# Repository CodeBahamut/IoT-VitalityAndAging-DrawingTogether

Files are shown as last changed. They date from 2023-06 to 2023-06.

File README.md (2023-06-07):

# VitalityAndAging - Drawing Together

Studies have shown that it is important for elderly people to keep their creative brain activated. But for some elderly people it is harder to participate in creative activities. And that is why we are designing the Drawbot.

The Drawbot is a robot that can draw together with people. It reacts on what someone has drawn and uses unique movement to make wonderful art. This way elderly people will be able to use their creative brain and improve their cognitive skills without them spending hours having to physically draw.

Current Project Goals For this project we are going to do a lot of research on the technical options and availabilities of the Jetbot. After the research we want to have a Drawbot with the following end goals:

## Markdown Pages Site
To see a more clear site which is more clear and where we put a lot of effort into organizing the information click on this [Pages Link](https://iot.dev.hihva.nl/2022-2023-sep-jan/group-project/vitalityandaging-drawing-together/). For those who just want to browse through the repository look below. 

## Jetbot
Our Drawbot is based on the [Jetbot](https://jetbot.org/master/), we used the body of the Jetbot and modified to our needs by including a penholder that can lift and lower the pen using a servo. We also added an extension to the camera holder to accommodate the changes. We also added a base plate at the bottom to hold the Wemos D1 Mini which is controlling the servo and of course the servo itself. 

## Guide

To find information documentation related to the setup of certain parts and to follow the things we did go to [documentation](./docs/documentation/).

For information on the decisions we made and why we made them and thus the research we did to come to our conclusions go to [research](./docs/research/).

For the product manual go to [product manual](./docs/product_manual.md).
As for the bill of materials you can follow this [link](./docs/bill_of_materials.md).

## Build/Assembly guide

To find out how to build the Drawbot go to the [product manual](./docs/product_manual.md). There you will instructed on the adjustments you need to make to the [Jetbot](https://jetbot.org/master/). Of course you first need the [Jetbot](https://jetbot.org/master/) to be able to follow this guide.

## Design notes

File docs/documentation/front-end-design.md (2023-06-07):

# Front-end design
For the front-end design, we created a wireframe in figma.

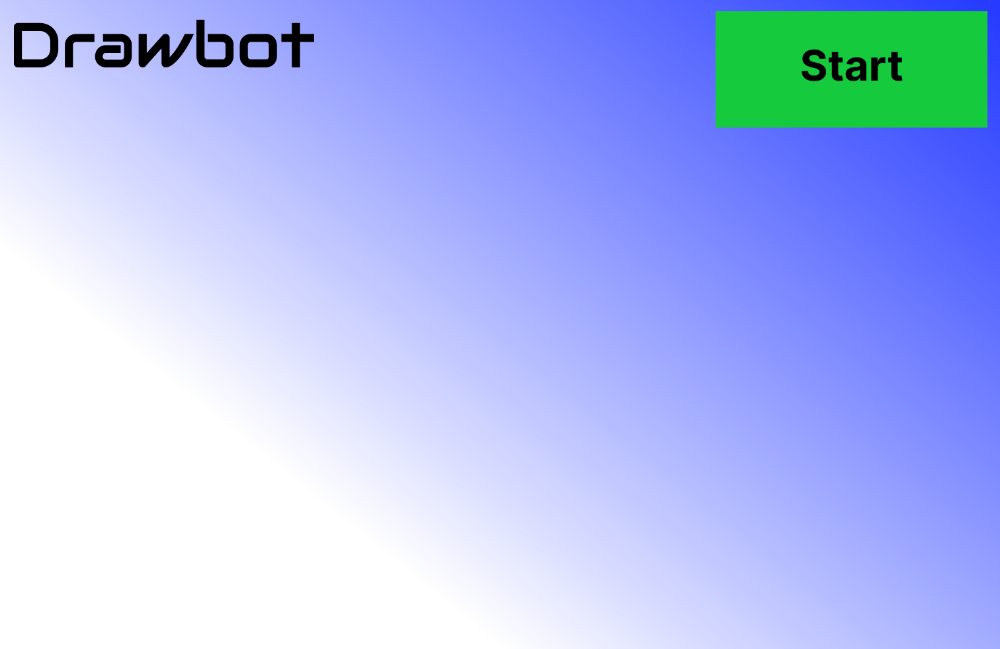
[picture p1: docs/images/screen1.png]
Screen 1

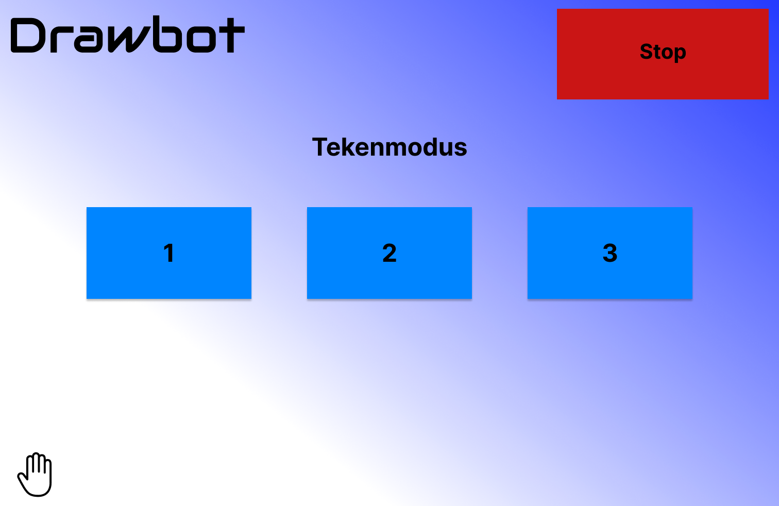
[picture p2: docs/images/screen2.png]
Screen 2

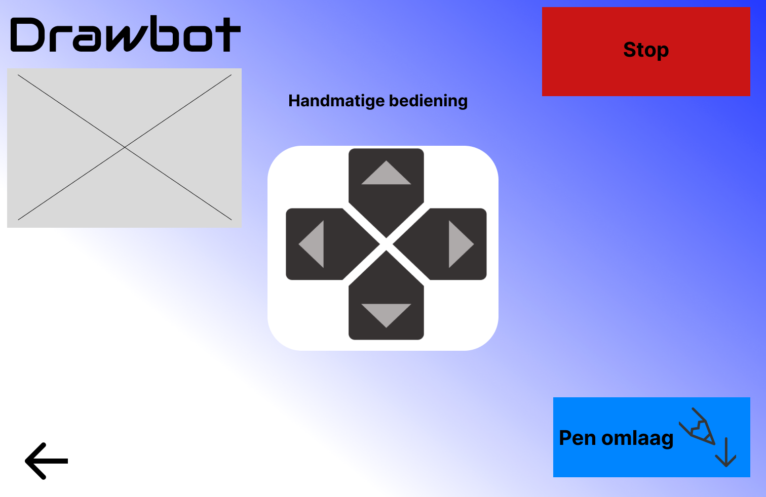
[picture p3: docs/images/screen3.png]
Screen 3


These are rough sketches of what the pages will look like.

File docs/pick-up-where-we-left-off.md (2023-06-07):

# Pick up where we left off

For the next team we advise to go through all the research and documentation we have made. Learn from our mistakes and
improve the DrawBot.

## Project code

[Here](https://gitlab.fdmci.hva.nl/IoT/2022-2023-sep-jan/group-project/vitalityandaging-drawing-together/-/tree/main/embedded-device/drawbot-server-latest-version/drawbot-s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)
you can find the code.

## Our issues

- The power, we noticed that when you're trying to draw and detect shapes at the same time the Drawbot has power issues.
  For more info on the power issues please look into [Power issues](documentation/power_issue.md)
- When we first got the Jetbot it was really hard to connect to it. We have made this way easier, have a look
  into [Jetbot configuration](documentation/jetbot_configuration.md) to set it up.

## Our advice

- We noticed that it is really hard for the Drawbot to make accurate drawings. The motors are not precise enough and
  there is too much fluctuation in the results. Our advice for this would be to use stepper motors. With stepper motors
  you can tell the Drawbot the exact amount of steps it should make. Which should result in more accurate drawings.

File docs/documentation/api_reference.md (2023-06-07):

### API reference

In this table below are all the API calls that can be made to the Drawbot server and some info about them.
Once connected to the hotspot, the Drawbot's server can be reached on jetbot.local:5000

| Endpoint | HTTP METHOD | Description | Response | 
|:---|:---|:---|:---:|
| / | GET | This will return the index page |  HTTP/1.1 200 OK<br>rendered html template (index.html page)  |
| /video | GET | This will push dynamically updated content to the web browser, which is used for streaming the camera's frames | HTTP/1.1 200 OK<br> multipart/x-mixed-replace; boundary=frame |
| /start | POST | This will kick off the Drawbot, by starting a separate thread that will handle the controllers | HTTP/1.1 200 OK<br>{"isDrawBotOn ": "True"} |
| /stop | POST | This will dispose the running thread that is responsible for handling the controllers | HTTP/1.1 200 OK<br>{"isDrawBotOn ": "False"} |
| /start-shape-detection | POST | This will start the shape detection mode, by starting a separate thread that is used to run the shape recognition  | HTTP/1.1 200 OK<br>{"shouldDetectShape ": "True"} |
| /stop-shape-detection | POST | This will stop the shape detection mode, by disposing the thread that is used to run the shape recognition | HTTP/1.1 200 OK<br>{"shouldDetectShape ": "False"} |
| /command/enqueue<br/>/command-type | POST | This will either enqueue or directly fire a certain command, (command-type can be: left, right, forward, backward) | HTTP/1.1 201 OK<br>{"isEnqueued ": "True/False"} |
| /draw-bot-state | GET | This will return the status of the Drawbot | HTTP/1.1 200 OK<br>{"isDrawBotOn ": "True/False"} |
| /pen-up | POST | This will send a signal to the Wemose, to set the pen up | HTTP/1.1 200 OK<br>{"isPenUp ": False} |
| /pen-down | POST | This will send a signal to the Wemose, to set the pen down | HTTP/1.1 200 OK<br>{"isPenUp ": True} |
| /flower-1 | POST | This will make the Drawbot to draw a flower v1 | HTTP/1.1 200 OK<br>{"drawing-flower-1": True} |
| /flower-2 | POST | This will make the Drawbot to draw a flower v2 | HTTP/1.1 200 OK<br>{"drawing-flower-2": True} |
| /flower-3 | POST | This will make the Drawbot to draw a flower v3 | HTTP/1.1 200 OK<br>{"drawing-flower-3": True} |

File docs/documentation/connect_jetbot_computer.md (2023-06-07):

# How to connect Jetbot to a computer

### Installing OS

If the Jetbot has the OS already installed on the SD card and configured you can skip this part.
If not click on the drop down menu below and follow the steps.

<details>
<summary> How to install OS and flash it onto SD card </summary>
<br> 

### Step 1

Go to the [Jetbot doc site](https://jetbot.org/master/software_setup/sd_card.html) and the Jetbot SD card image. The Jetbot for our project has the Jetson Nano (4GB) so make sure you choose the correct download file. 

### Step 2 

1. Insert an SD card into your desktop machine

2. Using [Etcher](https://www.balena.io/etcher/), select the image you downloaded above and flash it onto the SD card.

3. Remove the SD card from your desktop machine

</details>

### Boot Jetson Nano 

1. Insert the SD card into your Jetson Nano (the micro SD card slot is located 
   under the module)

2. Connect the monitor, keyboard, and mouse to the Nano

3. Power on the Jetson Nano by connecting the micro USB charger to the port

### Connecting to Wifi

Next you'll need to connect to WiFi.

1. Log in using the user ``drawbot`` and password ``Drawbotteam01``.
   If you're doing this off a fresh install the user is ``jetbot`` and password ``jetbot``.

2. Connect to a WiFi network using the following command

    ```bash
    sudo nmcli device wifi connect <SSID> password <PASSWORD>
    ```

Your Jetson Nano should now automatically connect to the WiFi at boot and display it's IP address on the piOLED display.

### Connect to Jetbot using browser

1. Shutdown JetBot using the command line

    ```bash
    sudo shutdown now
    ```

2. Unplug your HDMI monitor, USB keyboard, mouse and power supply from Jetson Nano

3. Power the JetBot from the USB battery pack by plugging in the micro-USB cable

4. Wait a bit for JetBot to boot

5. Check the IP address of your robot on the *piOLED* display screen.  Enter this in place of ``<jetbot_ip_address>`` in the next command

6. Navigate to ``http://<jetbot_ip_address>:8888`` from your desktop's web browser. You can do this from any machine on your local network.  

7. Sign in using the password ``Drawbotteam01`` (if that doesn't work try ``jetbot``).

You will be presented with a view similar to the following. 

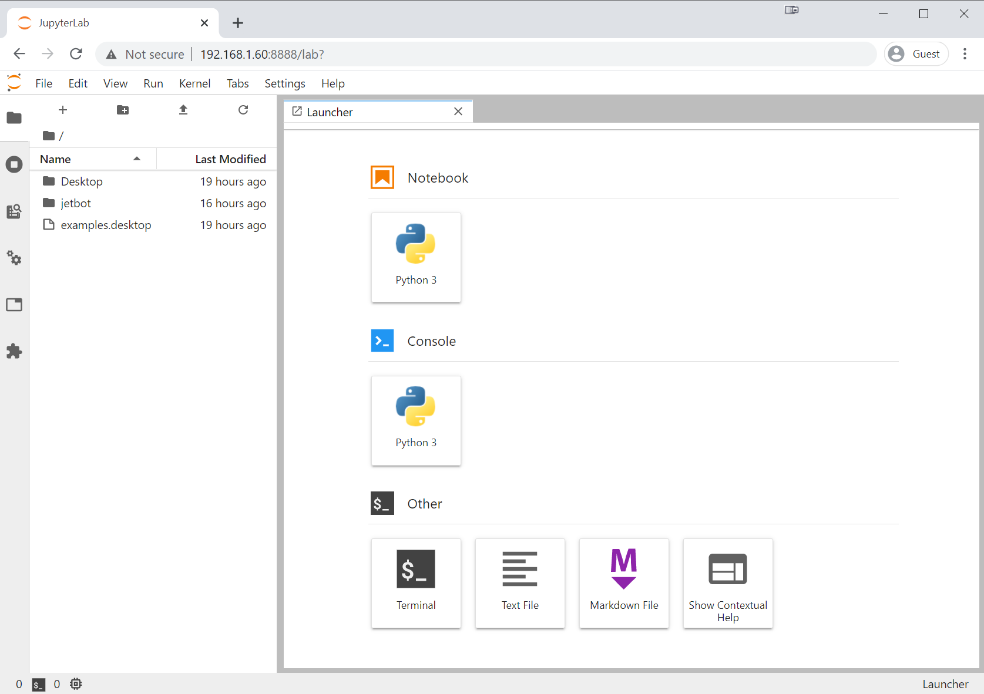
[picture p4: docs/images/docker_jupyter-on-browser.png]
jupyter on browser


From this point on, when you power on the JetBot, it should automatically connect to WiFi and display it's IP address.  So all you need to do is reconnect using your web browser to start programming!

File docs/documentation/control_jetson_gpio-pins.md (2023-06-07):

# Controlling the GPIO pins on the Jetson Nano 

### RPi GPIO

After following the guide below we managed to figure out how to control the GPIO pins on the Jetson nano. The OS comes with the RPi.GPIO library and if not you need to install it.

<iframe width="280" height="160" 
src="https://www.youtube.com/embed/BBKpEgJKF0s" 
title="YouTube video player" frameborder="0" allow="accelerometer;
autoplay; clipboard-write; encrypted-media; gyroscope; picture-in-picture" allowfullscreen></iframe>

Using this video I came up with the code for the next example.

```python
import RPi.GPIO as GPIO
import time   
class PenServo:
    
    def __init__(self, pin):
        self.pin = pin
        # Optional cleanup which resets GPIO states
        GPIO.setmode(GPIO.BOARD)
        GPIO.cleanup(pin)
        # Setup
        GPIO.setup(pin,GPIO.OUT)
        self.is_up = True
        
    def up(self, delay = 0):
        GPIO.output(self.pin,True)
        time.sleep(delay)
        self.is_up = True
        
    def down(self, delay = 0):
        GPIO.output(self.pin,False)
        time.sleep(delay)
        self.is_up = False
```

Here we use the RPi GPIO library to control the pins. Then we set the mode to board mode. Which means that you give it the pin numbers that are visible on the actual board. 
We cleanup the code to make sure its hasn't been configured or used for something else at the same time. We then set it as an output pin. We also add a state variable in the form of is_up to keep track of weather the servo is facing up or down. According to the code that we have on the Wemos if the pin is positive it will go up and if its negative it will go down. 

Below is an example using Jetson GPIO but we found this to be less intuitive than RPi.GPIO so we didn't use but it might prove handy for someone else. 

[NVIDIA/jetson-gpio](https://github.com/NVIDIA/jetson-gpio)

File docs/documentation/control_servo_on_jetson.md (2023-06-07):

# Servo on the Jetson Nano

In this documentation we will explain how we went about trying to get a servo working on the Jetson Nano, where we looked, 
what we found, what we ended up doing and the conclusion we came to. 

## Using the Wemos D1 to Control the servo according to a signal from the Jetson Nano. 

We use a Wemos D1 mini to control the servo while it receives a signal from the Jetson Nano. In our use case we only need the servo to switch between 2 states. So we came to the conclusion that 1 pin signal is enough since if we switch the signal from positive to negative thats 2 states and that fulfills our requirement. We used the GPIO pin to send a signal to the Wemos. For an explination on how we used the GPIO pins go to [Jetson GPIO pins.](documentation/control_jetson_gpio-pins.md) 

On the Wemos we used the following code 

```cpp
#define COMMAND_PIN D2
#define SERVO_PIN D4
#include <Servo.h>
Servo servo;

// the setup routine runs once when you press reset:
void setup() {
  Serial.begin(115200);
  pinMode(COMMAND_PIN, INPUT_PULLUP);
  servo.attach(SERVO_PIN);
}

// the loop routine runs over and over again forever:
void loop() {
  // read the input pin:
  int inputState = digitalRead(COMMAND_PIN);
  // print out the state of the servo:
  Serial.println(inputState);
  if(inputState == HIGH){
    servo.write(180);
    delay(1000);
  } else if(inputState == LOW){
    servo.write(0);
    delay(1000);
    } 
}
```

As you can see we assign pin D2 on the servo to the pin from the Jetson Nano so essentially its the input pin. While we assign pin D4 to the servo to control it. 
We then setup the input pin as a pullup so that we can get a consistent reading. We then print out the state for debugging purposes and we make a if statement for it to check weather the pin is on high or low and move the servo accordingly. 

For the Jetson nano side we made a class to control the pin.

```python
import RPi.GPIO as GPIO
import time   
class PenServo:
    
    def __init__(self, pin):
        self.pin = pin
        # Optional cleanup which resets GPIO states
        GPIO.setmode(GPIO.BOARD)
        GPIO.cleanup(pin)
        # Setup
        GPIO.setup(pin,GPIO.OUT)
        self.is_up = True
        
    def up(self, delay = 0):
        GPIO.output(self.pin,True)
        time.sleep(delay)
        self.is_up = True
        
    def down(self, delay = 0):
        GPIO.output(self.pin,False)
        time.sleep(delay)
        self.is_up = False
```

For an explication on how it works you can go again to our documentation on [Jetson GPIO pins.](documentation/control_jetson_gpio-pins.md) 

The wiring diagram is: 

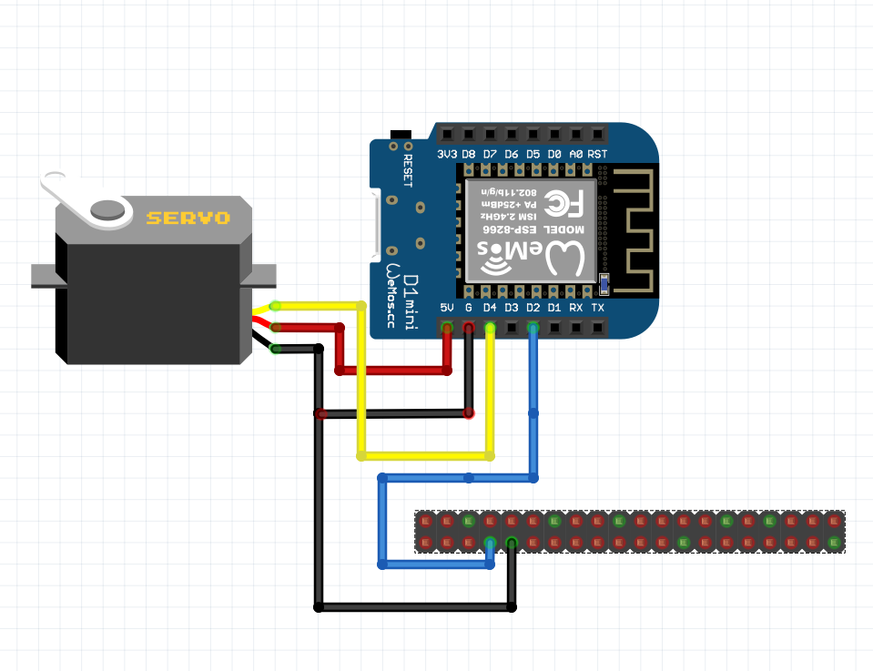
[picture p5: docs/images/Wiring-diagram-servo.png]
Wemos-Jetson-Wiring-Diagram


## Failed Attempt 1: Connecting servo directly to Jetson Nano

Initially we tried to connect the servo directly to the Jetson nano. After some research we found a few ways to do it. 
The first way was to turn on one of the PWM pins on the Jetson nano which do exist but they are disabled by default. 
The second method was to use the PCA9685 PWM module which is a module for adding servos to an embedded device if you 
lack PWMs or if you just want more than you currently have. 

We tried to turn on the PWMs pins by configuring the Jetson expansion headers using with the method on the
[nvidia Jetson nano documentation](https://docs.nvidia.com/jetson/archives/r35.1/DeveloperGuide/text/HR/ConfiguringTheJetsonExpansionHeaders.html). 

This didn't work and every time we tried to run the jetson-io.py file we would get an error. 
We tried to attempt to change the files ourselves without running the file, but we didn't get it working. 
After 2 days of tinkering with it, we came to the conclusion that because of the custom OS of the Jetbot 
we lacked certain directories/dependencies to get it to work, so we moved on to the next method.
gave up and tried the next method. 

Here are some sources we tried using that didn't fix our problem but did provide a lot of guidance:

[Jetson Nano Developer Kit User Guide](https://developer.nvidia.com/embedded/downloads#?search=Jetson%20Nano%20Developer%20Kit%20User%20Guide)

<iframe width="280" height="160" 
src="https://www.youtube.com/embed/eImDQ0PVu2Y" 
title="YouTube video player" frameborder="0" allow="accelerometer;
autoplay; clipboard-write; encrypted-media; gyroscope; picture-in-picture" allowfullscreen></iframe>

## Failed Attempt 2: Connecting the servo to the Jetson Nano using a PCA9686 PWM module

After our first failed attempt we ordered the module and tried running it with the Jetson Nano. 
We ran into 2 major problems with this module. 

The first one was that we got errors caused by the python version we were using. We thought about updating it but because we were using TensorRT and it needed other libraries and dependencies tp be a certain version or release which meant we couldn't just randomly update the python version. 

When we tested the I2C connection to the PCA9686 we got a response and confirmed that the Jetson was able to see it. We downloaded circuit python to use the adafruit-servokit library. But here we got the errors related to the python versions and we couldn't find a feasible solution. We also had problems related to the GPIO rules, to control the permissions we needed to adjust the gpio rules files but that file wasn't there with our version of the OS. So we ended up scraping this idea and decided to use a Wemos D1 mini to control the servo.

Here are some sources we tried using that didn't fix our problem but did provide a lot of guidance:

[Circuit Python Guide](https://learn.adafruit.com/circuitpython-libraries-on-linux-and-the-nvidia-jetson-nano/initial-setup)

[https://github.com/JetsonHacksNano/ServoKit](https://github.com/JetsonHacksNano/ServoKit)

<iframe width="280" height="160" 
src="https://www.youtube.com/embed/RnGUTny1hG8" 
title="YouTube video player" frameborder="0" allow="accelerometer;
autoplay; clipboard-write; encrypted-media; gyroscope; picture-in-picture" allowfullscreen></iframe>

<iframe width="280" height="160" 
src="https://www.youtube.com/embed/28Hj8if8fNY" 
title="YouTube video player" frameborder="0" allow="accelerometer;
autoplay; clipboard-write; encrypted-media; gyroscope; picture-in-picture" allowfullscreen></iframe>

<iframe width="280" height="160" 
src="https://www.youtube.com/embed/8YKAtpPSEOk" 
title="YouTube video player" frameborder="0" allow="accelerometer;
autoplay; clipboard-write; encrypted-media; gyroscope; picture-in-picture" allowfullscreen></iframe>

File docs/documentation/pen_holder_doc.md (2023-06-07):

### Sprint 1

In this documentation file we will explain how we made the pen holder extension for the JetBot. First we downloaded the original JetBot files from their [markdown page](https://jetbot.org/master/bill_of_materials.html) and loaded them into Fusion360 and Tinkercad. Because we did not yet know which software we were going to use we tried both. As Fusion360 is the most elaborate program we thought that would be the best option. The only downside of Fusion360 is that there is a big learning curve to learn the functions required to make the design. The downside of Tinkercad is that you can only create basic shapes. We divided the programs between two of the teammates and the person who was working with Tinkercad soon found out that creating a design with Tinkercad worked perfect. So we continued with that. 

After loading the original files into the program we discussed how we were going to attach a pen to the previously researched best location in between the wheels of the Bot. We soon found out that it was far too difficult to place the pen exactly in the middle because we then had to move the Jetson Nano and the battery. So we concluded that we would move the camera mount further to the front and place the pen behind it in front of the robot. Here is an image with a rough sketch of how we wanted it to turn out.

Rough sketch

What we did in this step is load in 2 camera mounts. With one we chopped off the top and with the other we chopped off the bottom so we could rotate the mount. We knew we wanted no limitations in what kinds of writing material we could use so we made a practice pen (the invisible cilinder you see) 2cm in diameter. From this we knew how far we needed to place the camera mount. 

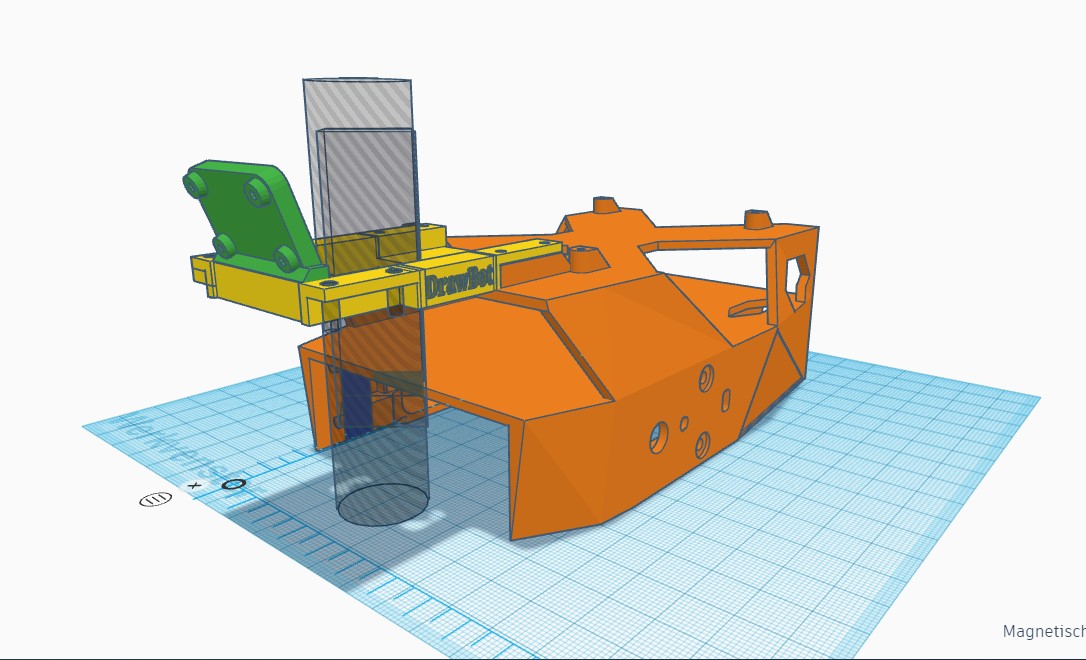
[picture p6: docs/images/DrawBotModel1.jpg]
Extensions complete


In the image above you can see how we attached the extension to the JetBot. We did this by loading in another camera mount and bridging the gap between those two with a box section. For added detail we put the text "DrawBot" on there. After that we filled in the space between those box sections and made a circular hole to fit the marker in. This was a 2cm diameter hole, this because the biggest marker is about that size so there would not be any restrictions. When that hole was created we started thinking of ways to fasten the marker on the design. We quickly came up with a system where two triangular cutouts could keep the marker in place after which a bolt of some sort could be tightened to squeeze against the marker to stop it from sliding out. These triangular cutouts are also useful when you want to install a different size pencil because the smaller the pencil the further it would get to the tip of the triangle.

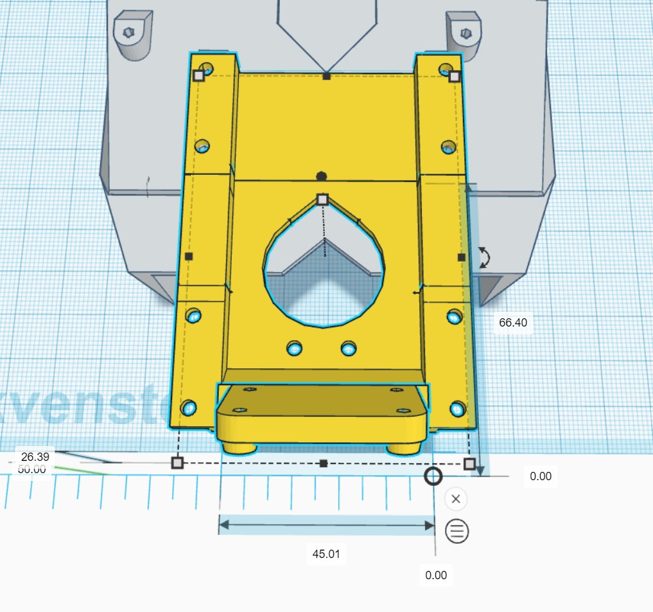
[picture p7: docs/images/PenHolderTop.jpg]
Cutout for the marker


Then we needed to make sure the whole design would not wiggle so the pen could not skip around on the paper. To achieve this we made use of 4 existing holes on the bottom of the JetBot and attached diagonal supports to it. We wanted these to resemble the structure of the JetBot which meant a lot of diagonal angles. This was a bit of a challenge to make in Tinkercad because of the limitation to normal shapes. But with some messing around we managed to get the supports diagonal from the side and from the front. 

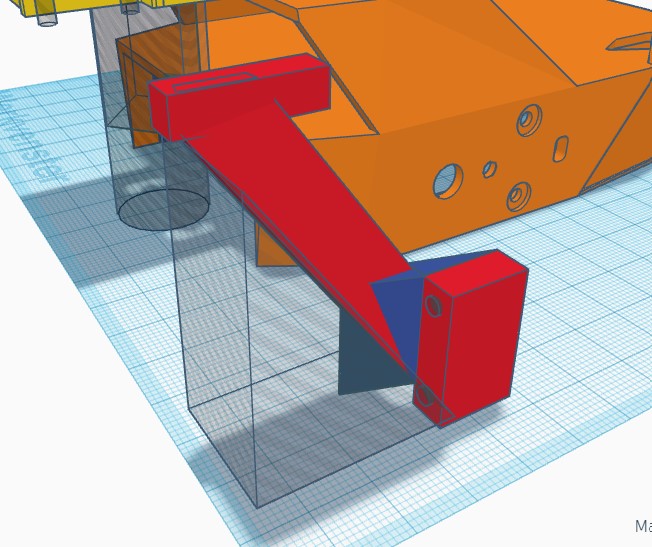
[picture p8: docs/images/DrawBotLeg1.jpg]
Drawbotleg1

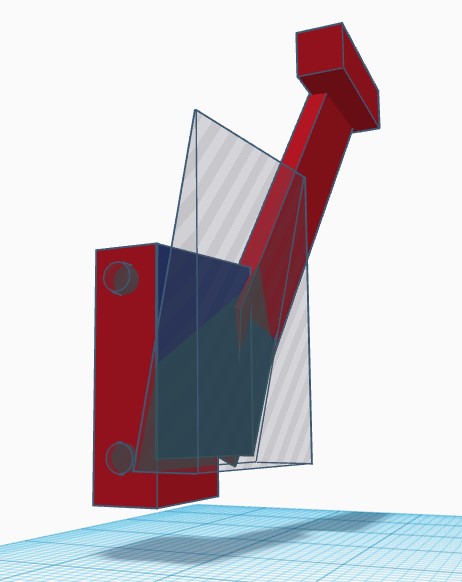
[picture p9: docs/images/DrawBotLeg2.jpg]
Drawbotleg2


In the images above you can see one of the legs that holds the camera mount steady. We made this by rotating a rectangular beam about 45 degrees and then attach it to two triangular shapes (blue bits). Aftre this we cut away the excess material by combining the support with two triangular holes as seen in the image. We copied and rotated one leg to fit on the other side. This in how the supports turned out.

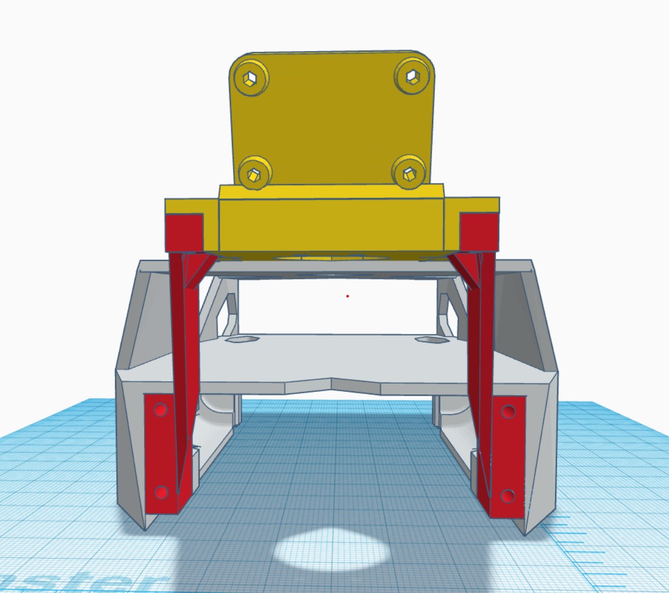
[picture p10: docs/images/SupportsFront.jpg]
SupportsFront

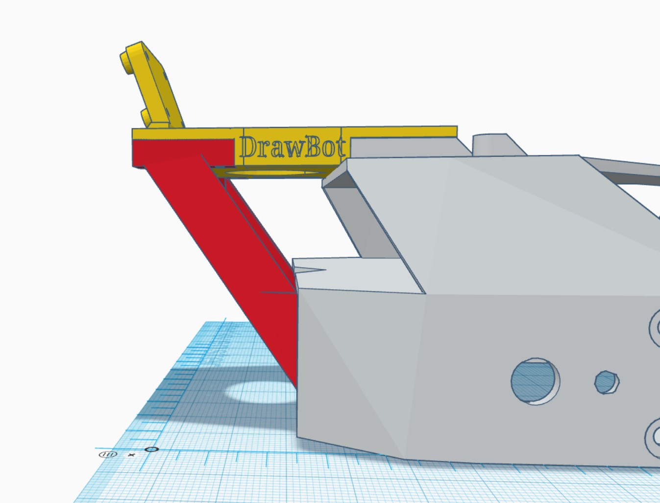
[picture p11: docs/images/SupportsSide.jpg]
SupportsSide


Lastly we needed to figure out a way to attach the bolt which squeezes against the marker. At first we wanted to make a hole just underneath where the camera sits but we came to the conslusion that the bolt would only press the marker against the top triangle and it would wiggle freely on te bottom triangle. So we made a little underhang with a hole big enough for the bolt and attached it using screws. Unfortunatly the first design we made was not big enough to put the bolt through and still be able to twist it with your fingers so we had to make it bigger. 

Failed Wedge

We made the wedge bigger to be more sturdy and so it could fit an M5 bolt. We decided that the M5 bolt should be a hex bolt because of the relatively smaller head. The only dwonside of a hex bolt is that its head is round so you would not be able to grip it to twist is. To resolve this we made a slide-over system that would make the hex bolt easier to twist. These can be seen in the image below.

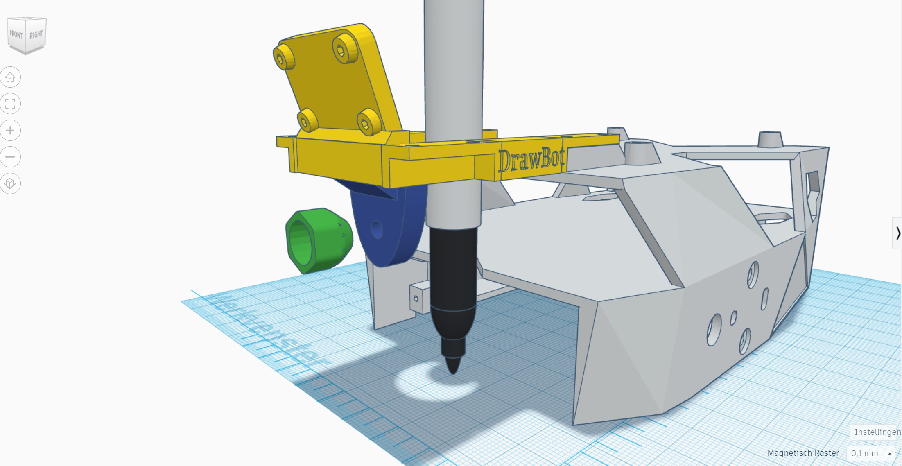
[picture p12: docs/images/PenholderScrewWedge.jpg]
ScrewWedge


All we had to do now was slice the design and print it. This process was no trouble as the program Ultimaker Cura created all the supports. One little mishap we noticed when the print was done was that we had placed the two legs the wrong way around so the program made printing supports on the outside. This turned out pretty ugly so we might change that later. You can click the black play button for a video.

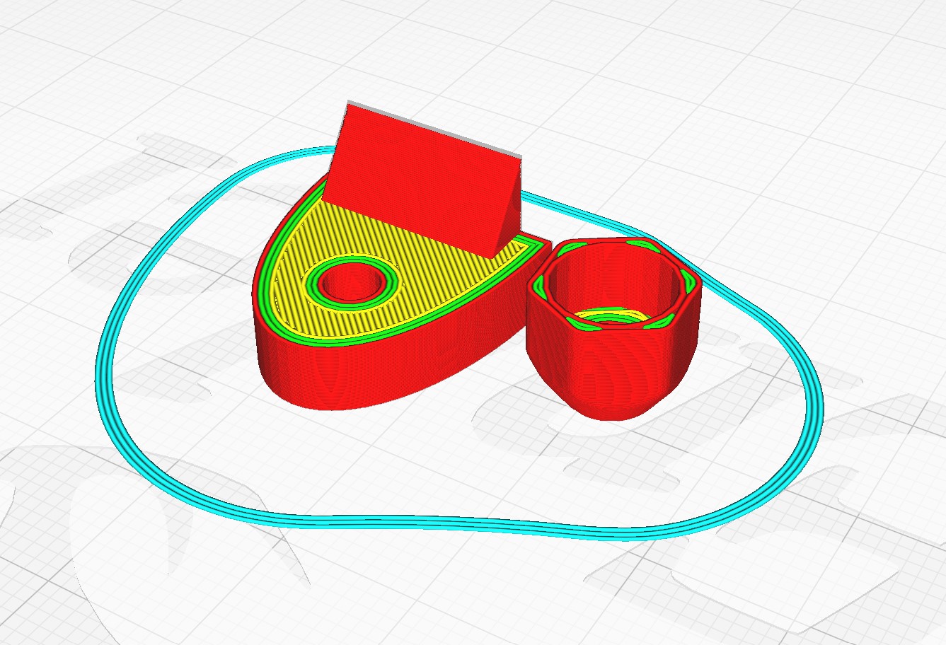
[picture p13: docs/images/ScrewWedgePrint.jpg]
WedgeScrewPrint

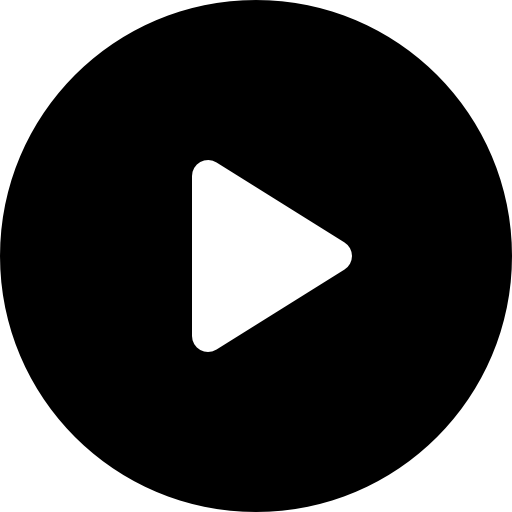
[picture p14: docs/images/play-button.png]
Penholderprint.MP4


<b>And after printing and attaching it looks like this!</b> 

HolderSide
HolderFront
HolderTop

It fit perfectly! There were no gaps and the screws could slide in like they had always been there. There were however some difficulties. The hole where the big screw fits through was not big enough to thread but this was resolved with brute force. The second issue was that the supports that were made for the 3d printer were too firm and were quite hard to remove. So after they were gone it looked like this:

Leg Before

We cleaned this up by wet sanding it and after that it turned out like this:

Leg After

### Sprint 2

For this sprint we want to change a couple of things:

- We need to be able to lift the pen off of the paper. This is going to be done with a servo.

- We need to get 4 M2 X 20 screws for the bottom of the legs, we could not find these anywhere. 

- And lastly we want to adjust the angle of the camera so it points more downward.

We started with adjusting the angle of the camera by loading the existing design in a new tinkercad file. Then we started to look around the design for how we could make the camera point down more. Soon we came up with a system where the camera could rotate so we could change the angle whenever we wanted to. This is what we came up with:

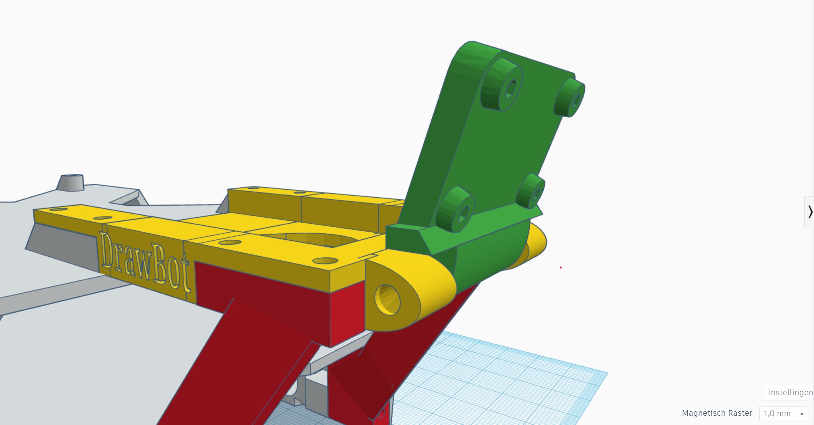
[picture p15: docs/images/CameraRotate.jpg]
Rotateable Camera


The idea is that there would be a bolt and a nut going through the holes. Once this is tightened the yellow part will clamp the green part holding the camera steady. We have not been able to test it as it is not done printing while this is being written. (Update: the model is done printing and it turned out pretty good. The only thing we had to do was make the holes a little bit bigger because the bolt would not slide through easily.)

After this was done we had to find a way to lift the pen off of the paper with a servo. We got inspiration from [this](https://youtu.be/tF2mantrnuI) video where the pen is in a seperate box. The box is on guides and is being pushed up by the servo and pushed down by springs. After some tinkering in Tinkercad it turned out like this: 

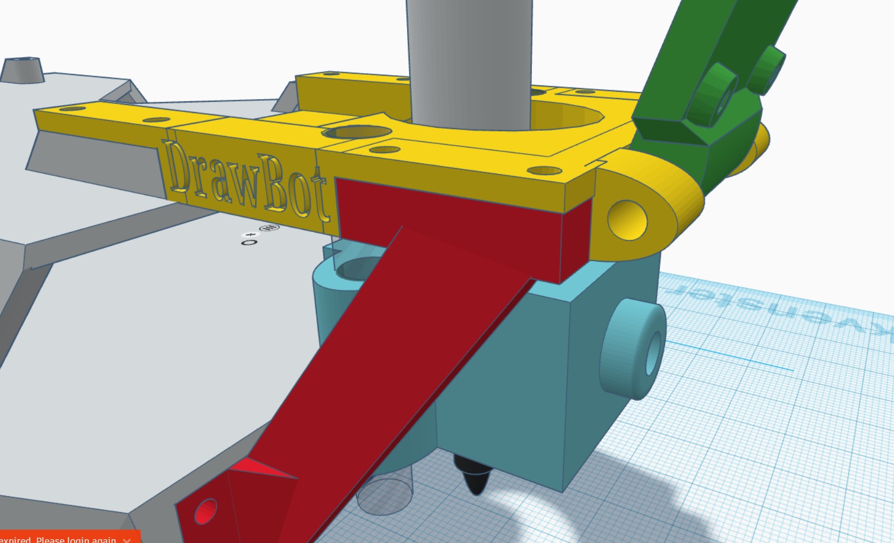
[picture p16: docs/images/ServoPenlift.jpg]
Pen lift side

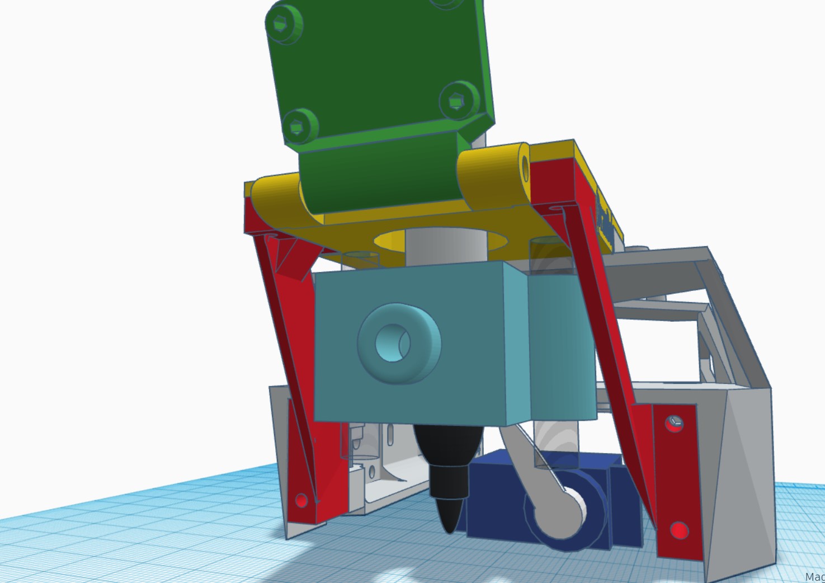
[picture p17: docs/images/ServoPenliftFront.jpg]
Pen lift front


The hole in the front of the light blue part is for an M5 bolt to clamp the pen in place. Just with the old design this part has a triangular hole so there is no limitation in what type of pen it fits. On the side of the blue parts there are two holes that are slightly bigger than an M6 bolt so that it can slide up and down. The bolts attach on the yellow part where we are going to tap the holes. If everything is sized properly the arm of the servo should just about hit the sliding part. 

After making this we had to find a way to attach the servo and the chip to control it. So we took another look at the existing JetBot and discovered 4 existing holes at the bottom. We used those to create a floor where the chip and servo could be attached. After designing it looked like this: 

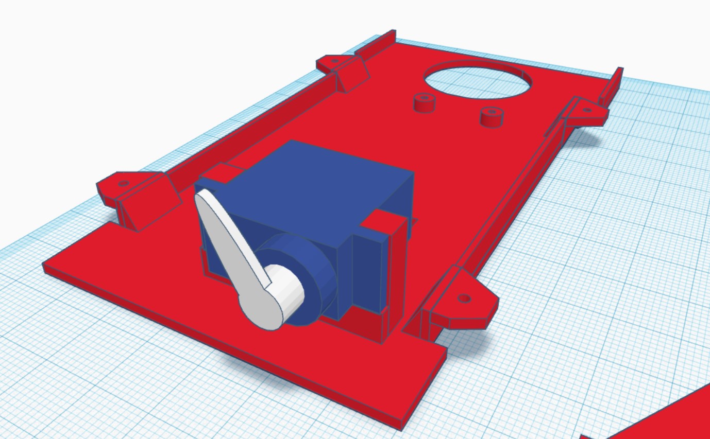
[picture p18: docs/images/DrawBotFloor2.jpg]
Floor


The floor is lower than the bottom of the JetBot because the chip we want to use is quite tall and when that is attached it hits the other chip that controls the motors. The servo uses its own mounting points.

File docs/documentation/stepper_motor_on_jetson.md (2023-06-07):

# Stepper Motors on the Jetson Nano 

## DC Motors vs Stepper Motors

### DC Motors

DC motors are electrical motors that move depending on the polarity of the magnets inside them. The polarity is determined by the the current that is flowing through it and the direction of the current. 

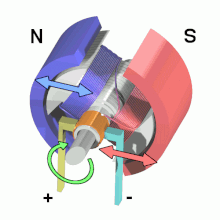
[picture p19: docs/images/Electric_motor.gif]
Electric Motor animation


As you can see in the animation above, the inside is covered in coils that change polarity depending on the direction of the current running through them and the outside are 2 magnets that repel/attract the magnets depending on their polarity. 

The fact that the DC motors can only be set on or off also means that they are hard to stop on a set point and thus hard to use for accurate movements. This fact is of importance to our project since we need accuracy to draw using the Drawbot. 

The video below goes more in depth on how electric motors work if you want to learn more. 

<iframe width="480" height="270" 
src="https://www.youtube.com/embed/CWulQ1ZSE3c" 
title="YouTube video player" frameborder="0" allow="accelerometer;
autoplay; clipboard-write; encrypted-media; gyroscope; picture-in-picture" allowfullscreen></iframe>

### Stepper Motors

Stepper motors work in principle the same as the DC motors. The main difference between the two is that DC motors have the coils mainly on the inside and the change in polarity happens in those coils to spin. While with the stepper motors the object with the set polarity is in the middle and the coils are on the outside ring. 

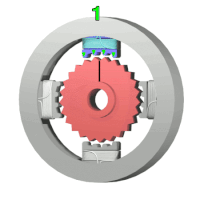
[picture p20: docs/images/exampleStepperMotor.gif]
Stepper Motor


As you can see in the example animation above the disk in the middle which is called the rotor gets spun around by changing the polarity of the motor which is called a stator. 

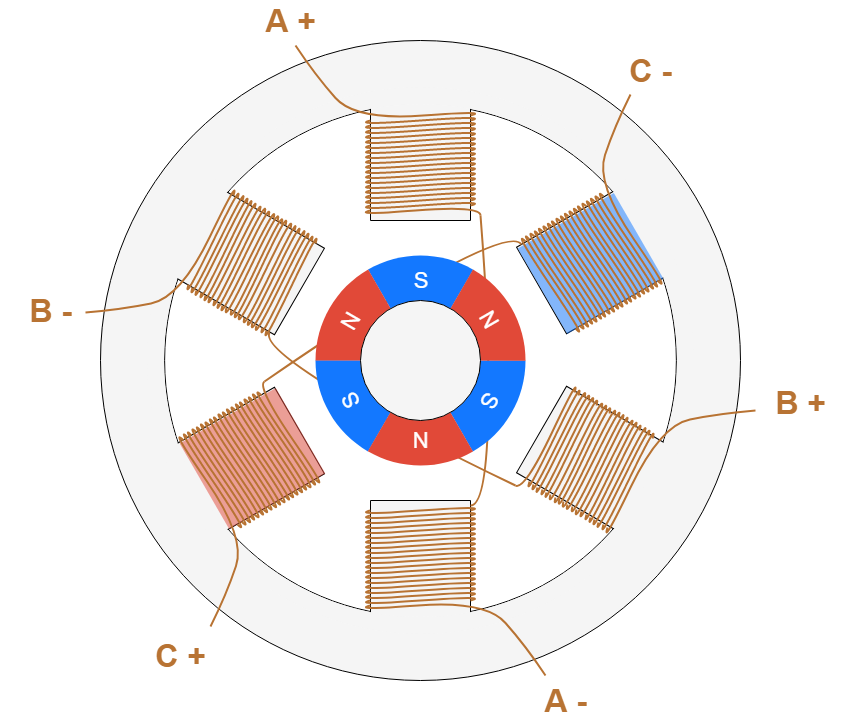
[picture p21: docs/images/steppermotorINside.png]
Inside Stepper motor


As shown here the rotor has more than polarity. The disk in the middle is split into pieces with different polaritys and by changing the polarity of the stator you can make the rotor spin step by step hence a stepper motor. Depends on how many times you split the rotor you can make it move smaller and smaller steps and hence get it more accurate. So for example with a stepper motor that needs 200 steps to make a full rotation you can determine that the accuracy of each step is 360 degrees/200 steps = 1.8 degrees per step. So with a stepper motor with 400 steps it would be 0.9 degrees per step.

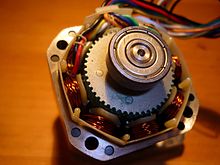
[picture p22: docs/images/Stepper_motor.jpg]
StepperMotor


This is the inside of a physical stepper motor for demonstration. 

For more info on how stepper motors work you can watch the video below.

<iframe width="480" height="270" 
src="https://www.youtube.com/embed/VfqYN1eG9Zk" 
title="YouTube video player" frameborder="0" allow="accelerometer;
autoplay; clipboard-write; encrypted-media; gyroscope; picture-in-picture" allowfullscreen></iframe>

### The pros and cons

__DC Motors__ are more useful for applications where the only goal is for the motor to keep spinning without an emphasis on accuracy. Take for a example dc motors in electric tooth brushes or fans. So their pro is that they can be turned on and they will keep spinning as long as power is provided. The con in this case is accuracy since they don't have a way to measure how far they spun like stepper motors do.

__Stepper Motors__ are more useful for precise applications. For example printers, 3D printers and the autofocus and zoom mechanisms in digital or phone cameras. The cons for stepper motors is that they are more complicated to use and that they are in general slower than normal dc motors.

### Why stepper motors are better for the Drawbot

In conclusion since stepper motors are able to move step by step while dc motors are only able to move on or off this means that stepper motors are way more accurate than normal dc motors. For our drawbot we want to be able to draw shapes and for that we need the robot to rotate in precise angles and that is not physically possible using just dc motors. So in conclusion we need stepper motors to get the drawbot to draw more accurately. 

## Kinds of stepper motors 

There are many kinds of stepper motors. Some with different sizes and some with more or less accuracy depending on the how many steps they take for a full rotation as explained above. For this project we would use the 28BYJ-48 stepper motor and ULN2003 driver board. 

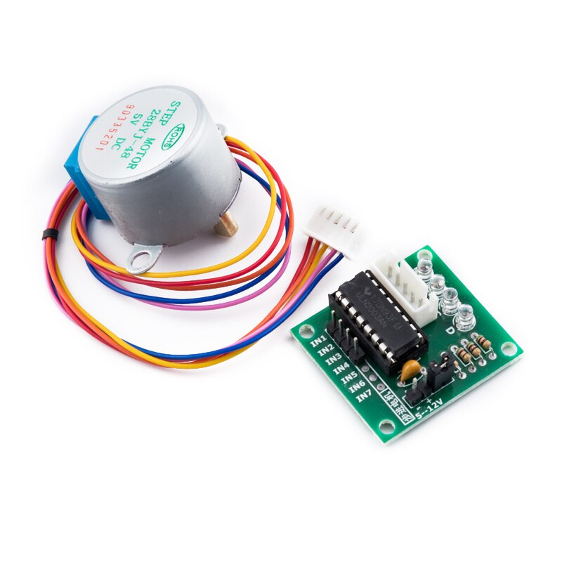
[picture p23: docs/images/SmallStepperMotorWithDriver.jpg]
28BYJ-48 stepper motor and ULN2003 driver board


These is one of the smaller stepper motors that you can buy and while being pretty cheap it should get the job done. 

## Connect Stepper Motor to Jetson

## Examples using an Arduino

While I was researching this I found two pretty encompassing guides that might be useful so I decided to share them below.

<iframe width="480" height="270" 
src="https://www.youtube.com/embed/CEz1EeDlpbs" 
title="YouTube video player" frameborder="0" allow="accelerometer;
autoplay; clipboard-write; encrypted-media; gyroscope; picture-in-picture" allowfullscreen></iframe>

<iframe width="480" height="270" 
src="https://www.youtube.com/embed/avrdDZD7qEQ" 
title="YouTube video player" frameborder="0" allow="accelerometer;
autoplay; clipboard-write; encrypted-media; gyroscope; picture-in-picture" allowfullscreen></iframe>

### Connecting stepper motor directly to Jetson

We researched ways to connect the Jetson directly to a stepper motor but non seemed to work for our use case and the biggest problem was that we would need to make use of the PWM pins on the Jetson which as mentioned in our [Jetson to servo documentation](../documentation/control_servo_on_jetson.md) we couldn't get to work previously with our current OS. 

### Using adafruit feather motor driver 

We can use the [adafruit stepper dc motor featherwing](https://learn.adafruit.com/adafruit-stepper-dc-motor-featherwing/downloads) 
to control the stepper motors. By using the circuit python library we can use the featherwing board to control the stepper motors. 

Using [this link](https://learn.adafruit.com/adafruit-stepper-dc-motor-featherwing/pinouts)
you can see the pin layout for the feather board. Below you can see a simplified version of the contents. 

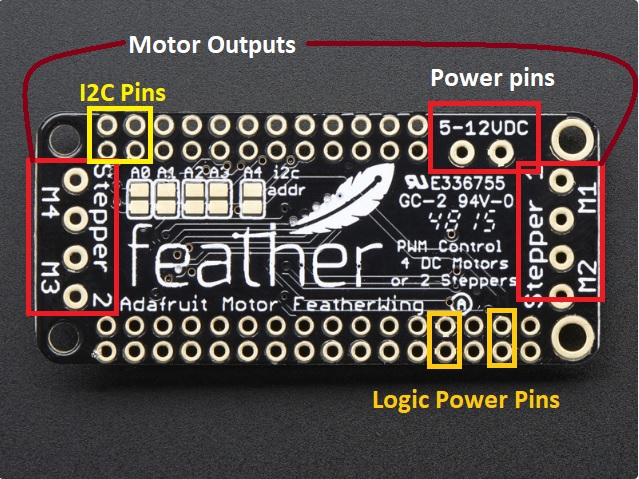
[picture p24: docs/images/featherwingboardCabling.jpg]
Featherboard pin layout


You can follow this [adafruit guide](https://learn.adafruit.com/adafruit-stepper-dc-motor-featherwing/using-stepper-motors) 
to use a stepper motor with the featherwing on an arduino. I am using this guide mainly to figure the cabling out. 

featherwingwithbigSteppr

[This is a guide](https://learn.adafruit.com/micropython-hardware-pca9685-dc-motor-and-stepper-driver/tdicola-hardware) using the 28BYJ-48 stepper motor. This guide is outdate but this is useable for inspiration and to figure out the cabling using the 28BYJ-48.

This [guide for using circuitpython with the feather board](https://learn.adafruit.com/adafruit-stepper-dc-motor-featherwing/circuitpython)
is what we are planning to use to control the stepper motors using the current drawbot setup we have using the Jetson nano. 

## Conclusion
 
If we were to try to use the Jetson nano to control the stepper motor we would go with the last method mentioned above which is using the featherwing board to control the stepper motor from the Jetson nano. We would try to get it working using the 28BYJ-48 stepper motor either directly to the board or using the ULN2003 driver board. We have to test which would work with the featherwing board. We have concluded that it is hard to know if this will work without testing and thus if we implement this into our project we will document the results and link it below.

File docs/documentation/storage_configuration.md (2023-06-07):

# Storage Configuration

## Issue that leads having 24GB instead of 64GB
When downloading the "jetbot-043_nano-4gb-jp45.zip" from v0.4.3 for jetbot (Jetson Nano (4GB)), and flash it by etcher successfully. But when the jJetbot is powered, only 
24G storage is available.
So to solve this issue please follow the given steps.

1. Download the pre-built JetBot SD card image
   Download the pre-built JetBot SD card image from the table below. Make sure to select the version that matches the
   Jetson you're using (for example Jetson Nano 2GB).

| Platform | JetPack version | Jetbot version | Response | MD5 Checksum |
|:---|:---|:---|:---:|:---:|
| Jetson Nano (4GB) | 4.5 | 0.4.3 | [jetbot-043_nano-4gb-jp45.zip](https://drive.google.com/file/d/1o08RPDRZuDloP_o76tCoSngvq1CVuCDh/view) | 760b1885646bfad8590633acca014289 |

!!! warning
    To utilize one of the JetBot SD card images based on JetPack 4.5, start your Jetson Nano with a plain JetPack 4.5 SD card image and go through the operating system setup. This will do a one-time setting that will allow you to utilize JetPack 4.5 SD card images on your device. Original JetPack SD card pictures may be found here: JetPack SD card image for Jetson Nano 2GB and JetPack SD card image for Jetson Nano (4GB). After you've completed this method, you may utilize the JetPack 4.5-based JetBot SD card images provided above on your device.

2. Flash JetBot image onto SD card
   Insert an SD card into your desktop machine

Using Etcher, select the image you downloaded above and flash it onto the SD card.

Remove the SD card from your desktop machine

3. Boot Jetson Nano
    - Insert the SD card into your Jetson Nano (the micro SD card slot is located under the module)
    - Connect the monitor, keyboard, and mouse to the Nano
    - Power on the Jetson Nano by connecting the micro USB (for Jetson Nano (4GB)) or USB-C (for Jetson Nano 2GB)
      charger to the port

!!! warning
    We recommend that you initially start the Jetson Nano without the piOLED or motor driver attached.
    This manner, you can ensure that the system boots successfully from the SD card image without having to worry about hardware concerns. After confirming that it boots, reattach the piOLED, double-check your wiring, and reboot.

!!! note
    Make sure that you have downloaded this Jetson Nano image: jetbot-043_nano-4gb-jp45.zip, the official documentation recommends other version which is 4.5.

4. Now you have to execute some commands
    - Go to Jetcard directory
      ```bash
      cd ~/jetcard
      ```
    - Pull the latest changes by executing this command
      ```bash
      git pull
      ```
    - Lastly, execute the pulled bash script
      ```bash
      ./script/jetson_install_nvresizefs_service.sh
      ```

To check whether the Jetbot is using the full size of the SD card, which is 64GB, run this command in the terminal<br>
```bash
df -h
```
you should see something like this

```bash
jetbot@nano-4gb-jp45:~$ df -h
Filesystem Size Used Avail Use% Mounted on
/dev/mmcblk0p1 64G 25G 35G 39% /
none 1.8G 0 1.8G 0% /dev
tmpfs 2.0G 4.0K 2.0G 1% /dev/shm
tmpfs 2.0G 19M 2.0G 1% /run
tmpfs 5.0M 4.0K 5.0M 1% /run/lock
tmpfs 2.0G 0 2.0G 0% /sys/fs/cgroup
tmpfs 397M 0 397M 0% /run/user/1000
```

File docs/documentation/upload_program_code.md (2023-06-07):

# How to upload program code to the Jetnano development board

This guide requires the following:

1. Doing all the steps of the [Setup Drawbot guide](connect_jetbot_computer.md)
2. A monitor with an HDMI or Display Port output
3. An HDMI or Display Port cable
4. A USB keyboard

## 1. Getting the Drawbot ip-address

You need the ip-address of the Drawbot to connect with it.

1. Enter the username

```bash
login: [JETBOT-LOGIN-GOES-HERE]
```

2. Enter the password

```bash
password: [JETBOT-PASSWORD-GOES-HERE]
```

2. Getting the ip-address

```bash
hostname -I
```

The result will be unique for everyone. You should see a result like

```bash
192.0.82.1
```

## 2. Connecting to the device wirelessly

Now that we have the ip-address, we can access the Jupiter Notebook environment of the Drawbot

1. Open your browser and go to the ip-address that you've obtained in the previous step like this:

```
[ip-address]:8888
```

You should see a screen popping up with the Jupiter Notebook logo. If the page doesn't load, something is wrong with the
internet connection.

2. Login with

```
jetbot
```

You are now connected with the Drawbot and able to add the program code.

## 3. Connecting to the device using micro-usb

This guide is a work in progress

In short:

1. Use a jumper wire to enable power using the DC-connector.
2. Plug in the DC-connector into a wall outlet. Plug the other end into the DC input on the Drawbot
3. Plug in a micro usb cable into the Drawbot. Plug the other end into your computer.

Next steps cannot be tested since we don't require a DC-connector.

### [Work in Progress]

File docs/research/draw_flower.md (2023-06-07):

# How can the Drawbot draw a flower?

We decided that the drawbot should draw a flower once it recognizes a circle. To make this happen, we have to decide how the flower can be drawn. Because we cannot make the rotations of the wheel motor consistent, it is impossible to make a perfect drawing. We can however input some commands which should represent a cool looking flower shape.

## Single leaf drawing

The drawbot is able to draw a single leaf of the flower. In the sketch below we have an example of this.

Drawbot leaf drawing

The drawbot detects the circle and starts the first leaf. It makes a small curve. When it has reaches a few centimeters, it turns quickly. Then, it makes another curved turn, resulting in the full leaf. Because the angle in which it turned is around 30 degrees, it can repeat this process 360/30, which is 12 times to make a full flower.

Doing it this way, we can program the Drawbot to check for new interpretations after each leaf is drawn.

### Drawbot code to draw a leaf

We have created 3 demo's of a circle. Because our motors are not consistent, creating a perfect flower is impossible. The source code can be found here:

```python
def drawSunflowerLeaf(self):
    INITIAL_SPEED = 0.4
    TIMEOUT = 0.25

    self.robot.forward(INITIAL_SPEED)
    sleep(TIMEOUT)

    self.robot.backward(INITIAL_SPEED)
    sleep(TIMEOUT)

    self.robot.left(INITIAL_SPEED)
    sleep(TIMEOUT)

    self.robot.stop()

def drawLeaf(self):
    INITIAL_SPEED = 0.6
    LEAVE_CURVE_TIMEOUT = 0.5
    TIMEOUT_TURN = 2.5
    SLOW_SPEED = INITIAL_SPEED * 0.3

    # Curve forward
    self.robot.set_motors(SLOW_SPEED, INITIAL_SPEED * 0.8)
    sleep(LEAVE_CURVE_TIMEOUT)

    self.setPenUp()
    self.robot.stop()
    sleep(2)

    # Turn
    self.robot.set_motors(0, INITIAL_SPEED)
    sleep(LEAVE_CURVE_TIMEOUT)
    self.robot.set_motors(-INITIAL_SPEED, 0)
    sleep(LEAVE_CURVE_TIMEOUT)

    self.setPenDown()
    self.robot.stop()
    sleep(2)

    # Curve forward
    self.robot.set_motors(SLOW_SPEED, INITIAL_SPEED * 0.8)
    sleep(LEAVE_CURVE_TIMEOUT)

    self.robot.stop()
        
def drawTurnLeafLeaf(self):
    INITIAL_SPEED = 0.6
    LEAVE_CURVE_TIMEOUT = 0.5
    TIMEOUT_TURN = 2.5
    SLOW_SPEED = INITIAL_SPEED * 0.3

    # Quick turn
    self.robot.set_motors(0, INITIAL_SPEED)
    sleep(LEAVE_CURVE_TIMEOUT)

    self.robot.set_motors(-INITIAL_SPEED, 0)
    sleep(LEAVE_CURVE_TIMEOUT)

    self.robot.stop()
```

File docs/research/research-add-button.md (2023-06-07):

# How to add a button to the Jetbot Nano

First we are going to connect the button and wires to the JetBot like so Jetbot button wiring diagram.

To test if the button is connected correctly we are going to open up the terminal. Run the following commands 1 by 1.

```cmd
python3
```
```cmd
import RPi.GPIO as GPIO
```
```
GPIO.setmode(GPIO.BOARD)
```
```cmd
GPIO.setup(15,GPIO.IN)
```
```cmd
x=GPIO.input(15)
```
```cmd
x
```
The output should be 1.

Now if you press the button and execute the x=GPIO.input(15) command again, the output should be 0.

When exiting the terminal make sure to use the following command.
```cmd
GPIO.cleanup()
```
This cleans all the pins, if you don't do this the gpio pin stays locked up.

Now that we know that our button works we are going to open up a new python file. 
```python
import RPi.GPIO as GPIO
GPIO.setmode(GPIO.BOARD)
inPin=15
GPIO.setup(inPin,15,IN)
while True:
    x=GPIO.input(inPin)
    print(x)
```
Now we can read out the pin and the button is connected! 

I used the following [tutorial](https://www.youtube.com/watch?v=ehzrPl5cNCc) to set up the button.

## Errors
While trying to run the command ``import RPi.GPIO as GPIO`` I found out that I needed to install the RPi module. To install the RPi module I first had to install pip. I had a lot of problems trying to install the library and couldn't get it to work. 

# How to use a button to turn the Jetbot on or off

On your Jetson Nano, you have to find the header pins they are located here: 
top view

Here you can see what the pins do:
header pins

1. First you have to use a jumper wire to prevent the Jetson Nano from auto powering on after you plug the cable in.
2. After that you can connect a button to pins 1 and 2. After shortening the pins the Jetson will power on or off.

Source for the documentation [Dots and brackets codeblog](https://codeblog.dotsandbrackets.com/power-buttons-jetson-nano/).

# Applying research to our project
After discussing with the team we decided that we didn't want the power on/off button to shut the whole Jetbot down. Instead we want to have a push button to just pause the Jetbot and stop moving. So that the Jetbot is still powered on and able to start drawing again. We came to the conclusion that a remote receiver would be a good option to pause the Jetbot.

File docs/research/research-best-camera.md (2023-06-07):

# What cameras are available for the Jetbot?

The current camera with the Jetbot is the Raspberry pi camera V2. We have experienced that the camera is having difficulties detecting colors due to change of lightning throughout the day. Hence why we are researching the available camera options for the Jetbot.

|Camera|Description|Model|MP|Price|
|:-----:|:-----:|:-----:|:-----:|:-----:|
|[Raspberry Pi v2](https://www.tinytronics.nl/shop/en/sensors/optical/cameras-and-scanners/raspberry-pi-camera-v2-8mp)|The standard camera that comes with most of the Jetbot kits.|RPICAMV2|8MP| €26.00|
|[IMX219 Camera Module, 160 degree FoV](https://www.waveshare.com/imx219-d160.htm)|A camera module for the standard raspberry pi v2 camera. The module epxands the FoV to 160 degrees.|IMX219-D160|-|$12.99|
|[Arducam 12MP IMX477 Mini High Quality Camera Module for Raspberry Pi](https://www.sossolutions.nl/arducam-12mp-imx477-mini-high-quality-camera-module-for-raspberry-pi)|A high quality upgrade to the Raspberry Pi v2. You can also switch out the lenses of the IMX477 camera.|IMX477|12,3|€94,95|
|[16MP IMX519 Autofocus Camera Module for Raspberry Pi](https://thepihut.com/products/arducam-imx519-autofocus-camera-module-for-raspberry-pi)| A cheap upgrade from the raspberry pi v2 with autofocus build in and higher MegaPixels.|IMX519|16|£24|

----
After researching the available camera options for the Jetson our best option would be the [16MP IMX519](https://thepihut.com/products/arducam-imx519-autofocus-camera-module-for-raspberry-pi). This camera is a noticeable upgrade from the [Raspberry Pi v2](https://www.tinytronics.nl/shop/en/sensors/optical/cameras-and-scanners/raspberry-pi-camera-v2-8mp) and because of the price this would be the most logical upgrade. The [12MP IMX477 ](https://www.sossolutions.nl/arducam-12mp-imx477-mini-high-quality-camera-module-for-raspberry-pi) would be the best available option if you want the highest quality but in my opinion that would be overkill in our project. Because the camera is pretty expensive and we don't need the option to switch out multiple lenses. All we need is a good quality camera that can detect lines, shapes and colors. Below you'll find a screenshot comparing the 3 different cameras. 
Comparing the 3 cameras

Source for the comparing image and research on the cameras [Jeff Geerling](https://www.youtube.com/watch?v=j2S8sZoH36Y).

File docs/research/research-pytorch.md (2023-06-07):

# PyTorch

## Introduction to Tensors
In machine learning, when representing the data, we need to do that numerically. A tensor is simply a container that can hold data in multiple dimensions. In mathematical terms, however, a tensor is a fundamental unit of data that can be used as the foundation for advanced mathematical operations. It can be a number, vector, matrix, or multi-dimensional array like Numpy arrays. Tensors can also be handled by the CPU or GPU to make operations faster. There are various types of tensors like Float Tensor, Double Tensor, Half Tensor, Int Tensor, and Long Tensor, but PyTorch uses the 32-bit Float Tensor as the default type.

## How to apply PyTorch

At its core, PyTorch provides two main features:

1. An n-dimensional Tensor, similar to numpy but can run on GPUs
2. Automatic differentiation for building and training neural networks

We will initially create the network in numpy before moving on to PyTorch.

Numpy includes an n-dimensional array object as well as several functions for manipulating these arrays. Numpy is a general-purpose scientific computing framework; it is unaware of computation graphs, deep learning, or gradients. However, by manually constructing the forward and backward traverses over the network using numpy operations, we can easily fit a third order polynomial to a sine function:

Numpy is a fantastic framework, however it cannot use GPUs to speed up numerical operations. GPUs frequently give speedups of 50x or larger for contemporary deep neural networks, hence numpy will not suffice for modern deep learning.

```python
# -*- coding: utf-8 -*-
import numpy as np
import math

# Create random input and output data
x = np.linspace(-math.pi, math.pi, 2000)
y = np.sin(x)

# Randomly initialize weights
a = np.random.randn()
b = np.random.randn()
c = np.random.randn()
d = np.random.randn()

learning_rate = 1e-6
for t in range(2000):
    # Forward pass: compute predicted y
    # y = a + b x + c x^2 + d x^3
    y_pred = a + b * x + c * x ** 2 + d * x ** 3

    # Compute and print loss
    loss = np.square(y_pred - y).sum()
    if t % 100 == 99:
        print(t, loss)

    # Backprop to compute gradients of a, b, c, d with respect to loss
    grad_y_pred = 2.0 * (y_pred - y)
    grad_a = grad_y_pred.sum()
    grad_b = (grad_y_pred * x).sum()
    grad_c = (grad_y_pred * x ** 2).sum()
    grad_d = (grad_y_pred * x ** 3).sum()

    # Update weights
    a -= learning_rate * grad_a
    b -= learning_rate * grad_b
    c -= learning_rate * grad_c
    d -= learning_rate * grad_d

print(f'Result: y = {a} + {b} x + {c} x^2 + {d} x^3')

```

The Tensor is the most fundamental PyTorch notion, and it is introduced here. A PyTorch Tensor is essentially equivalent to a numpy array: a Tensor is an n-dimensional array, and PyTorch includes several methods for working with Tensors. Tensors can maintain track of a computational graph and gradients behind the scenes, but they're also valuable as a general tool for scientific computing.

In addition, unlike numpy, PyTorch Tensors may use GPUs to speed numeric operations. To execute a PyTorch Tensor on GPU, simply supply the appropriate

```python
import torch
import math

dtype = torch.float
device = torch.device("cpu")
device = torch.device("cuda:0") # Uncomment this to run on GPU

Create random input and output data
x = torch.linspace(-math.pi, math.pi, 2000, device=device, dtype=dtype)
y = torch.sin(x)

Randomly initialize weights
a = torch.randn((), device=device, dtype=dtype)
b = torch.randn((), device=device, dtype=dtype)
c = torch.randn((), device=device, dtype=dtype)
d = torch.randn((), device=device, dtype=dtype)

learning_rate = 1e-6
for t in range(2000):

Forward pass: compute predicted y
y_pred = a + b * x + c * x ** 2 + d * x ** 3

    # Compute and print loss
    loss = (y_pred - y).pow(2).sum().item()
    if t % 100 == 99:
        print(t, loss)

    # Backprop to compute gradients of a, b, c, d with respect to loss
    grad_y_pred = 2.0 * (y_pred - y)
    grad_a = grad_y_pred.sum()
    grad_b = (grad_y_pred * x).sum()
    grad_c = (grad_y_pred * x ** 2).sum()
    grad_d = (grad_y_pred * x ** 3).sum()

    # Update weights using gradient descent
    a -= learning_rate * grad_a
    b -= learning_rate * grad_b
    c -= learning_rate * grad_c
    d -= learning_rate * grad_d

print(f'Result: y = {a.item()} + {b.item()} x + {c.item()} x^2 + {d.item()} x^3')
```

### PyTorch: nn
Computational graphs and autograd are a highly effective paradigm for creating complicated operators and automatically calculating derivatives; yet, raw autograd might be too low-level for big neural networks.

When designing neural networks, we typically consider layering the computation, with certain levels having learnable parameters that will be tuned during learning.

Packages like Keras, TensorFlow-Slim, and TFLearn in TensorFlow give higher-level abstractions over raw computational graphs that may be used to create neural networks.

The nn package in PyTorch provides the same function. The Modules defined by the nn package are generally comparable to neural network layers. A Module accepts input Tensors and computes output Tensors, but it may also store internal state, such as Tensors with learnable parameters. Below is an example of how the Pytorch nn works:

```python
# -*- coding: utf-8 -*-
import torch
import math

# Create Tensors to hold input and outputs.
x = torch.linspace(-math.pi, math.pi, 2000)
y = torch.sin(x)

# For this example, the output y is a linear function of (x, x^2, x^3), so
# we can consider it as a linear layer neural network. Let's prepare the
# tensor (x, x^2, x^3).
p = torch.tensor([1, 2, 3])
xx = x.unsqueeze(-1).pow(p)

# In the above code, x.unsqueeze(-1) has shape (2000, 1), and p has shape
# (3,), for this case, broadcasting semantics will apply to obtain a tensor
# of shape (2000, 3) 

# Use the nn package to define our model as a sequence of layers. nn.Sequential
# is a Module which contains other Modules, and applies them in sequence to
# produce its output. The Linear Module computes output from input using a
# linear function, and holds internal Tensors for its weight and bias.
# The Flatten layer flatens the output of the linear layer to a 1D tensor,
# to match the shape of `y`.
model = torch.nn.Sequential(
    torch.nn.Linear(3, 1),
    torch.nn.Flatten(0, 1)
)

# The nn package also contains definitions of popular loss functions; in this
# case we will use Mean Squared Error (MSE) as our loss function.
loss_fn = torch.nn.MSELoss(reduction='sum')

learning_rate = 1e-6
for t in range(2000):

    # Forward pass: compute predicted y by passing x to the model. Module objects
    # override the __call__ operator so you can call them like functions. When
    # doing so you pass a Tensor of input data to the Module and it produces
    # a Tensor of output data.
    y_pred = model(xx)

    # Compute and print loss. We pass Tensors containing the predicted and true
    # values of y, and the loss function returns a Tensor containing the
    # loss.
    loss = loss_fn(y_pred, y)
    if t % 100 == 99:
        print(t, loss.item())

    # Zero the gradients before running the backward pass.
    model.zero_grad()

    # Backward pass: compute gradient of the loss with respect to all the learnable
    # parameters of the model. Internally, the parameters of each Module are stored
    # in Tensors with requires_grad=True, so this call will compute gradients for
    # all learnable parameters in the model.
    loss.backward()

    # Update the weights using gradient descent. Each parameter is a Tensor, so
    # we can access its gradients like we did before.
    with torch.no_grad():
        for param in model.parameters():
            param -= learning_rate * param.grad

# You can access the first layer of `model` like accessing the first item of a list
linear_layer = model[0]

# For linear layer, its parameters are stored as `weight` and `bias`.
print(f'Result: y = {linear_layer.bias.item()} + {linear_layer.weight[:, 0].item()} x + {linear_layer.weight[:, 1].item()} x^2 + {linear_layer.weight[:, 2].item()} x^3')
```

## Conclusion
**NOTE** This research is not fully complete (since the author has solved the power issue in another ticket!).
has been applied on a stand-alone machine (not on the Jetbot), actually the merits of Tensorflow overweigh the ones of Pytorch.
There is no need to choose the Pytorch technique over Tensorflow, since our problem with Tensorflow is only having the power issue, which undoubtedly Pytorch has (because it also uses all the GPU cores for recognizing the objects). This problem could be solved by finding a way to limit the amount of used cores by the machine.

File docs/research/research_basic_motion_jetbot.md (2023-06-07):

## Step 1 Connect to the jetbot

To learn how to connect to the jetbot go to [connect jetbot to pc](..\documentation\connect_jetbot_computer.md)

## Step 2 Import Robot from jetbot

Assuming that we are using the Jetbot pre-built OS then its not that difficult to control the robot. 

First we should add the robot class from the jetbot package using the following line. 

```
from jetbot import Robot
```

The next step is to initilize it as an instance

```
robot = Robot()
```

## Step 3 Making the Jetbot move

### Giving simple movement commands to the Jetbot

The robot class has 4 basic automatized methods for movement (``left``, ``right``, ``forward`` and ``backward``). It also has a ``stop`` function. 

An example of using the forward method is:

```
robot.forward(0.1)
```

In this example 0.1 means 10% of its max speed. 

You can use the stop method in a similiar fashion:

```
robot.stop()
```

An example where you would make the robot go forward then stop using a short command would be:

```
robot.forward(0.5)
time.sleep(0.5)
robot.stop()
```

### Controlling motors individually

There are a few methods in the robot class to control the motors individually.

The first is ``set_motors``. Using this method you can give two values with the method. The first parameter is the value for the left motor and the second parameter is for the right motor. 

An example is as follows:

```
robot.set_motors(0.3, 0.1)
time.sleep(3.0)
robot.stop()
```

In this example the robot should go slowly to the right for 3 seconds then stop. 

Another method to to control the motors seperatly is by changing the values of the attributes of the motors inside of the robot class. The attributes for the motors are ``left_motor`` and ``right_motor``. So an example similiar to the one from eariler but using this method would be:

```
robot.left_motor.value = 0.3
robot.right_motor.value = 0.1
time.sleep(3.0)
robot.left_motor.value = 0.0
robot.right_motor.value = 0.0
```

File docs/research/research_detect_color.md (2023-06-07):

# How to detect a certain colour using Opencv

Firstly, analyzing a basic but important tool for identifying colors through a mask. We’re going to see in this video
how to detect colors through HSV Color space on Opencv with Python.

<iframe width="560" height="315" src="https://www.youtube.com/embed/Q0IPYlIK-4A" title="YouTube video player" frameborder="0" allow="accelerometer; autoplay; clipboard-write; encrypted-media; gyroscope; picture-in-picture" allowfullscreen></iframe>

HSV corresponds to:
Hue is the color
Saturation is the greyness
Value is the brightness

Understanding the concepts of balancing these three elements allows us to implement a basic color-based object
recognition system. Here blow is how to make a mask in a few simple steps to balance the recognition of our object in
real-time.
We import the Opencv and Numpy libraries, then load the cap to get the webcam frames. Following that, we begin a while
loop in which we obtain the frames and perform the detection.

```python
import cv2
import numpy as np
cap = cv2.VideoCapture(0)
while True:
    _, frame = cap.read()
    hsv_frame = cv2.cvtColor(frame, cv2.COLOR_BGR2HSV)
```

Within the while loop, we define the HSV ranges (low red, high red), create the mask, and display only the red objects.

```python
    # Red color
    low_red = np.array([161, 155, 84])
    high_red = np.array([179, 255, 255])
    red_mask = cv2.inRange(hsv_frame, low_red, high_red)
    red = cv2.bitwise_and(frame, frame, mask=red_mask)
```

Same for the other colors:

```python
    # Blue color
    low_blue = np.array([94, 80, 2])
    high_blue = np.array([126, 255, 255])
    blue_mask = cv2.inRange(hsv_frame, low_blue, high_blue)
    blue = cv2.bitwise_and(frame, frame, mask=blue_mask)
    # Green color
    low_green = np.array([25, 52, 72])
    high_green = np.array([102, 255, 255])
    green_mask = cv2.inRange(hsv_frame, low_green, high_green)
    green = cv2.bitwise_and(frame, frame, mask=green_mask)
    # Every color except white
    low = np.array([0, 42, 0])
    high = np.array([179, 255, 255])
    mask = cv2.inRange(hsv_frame, low, high)
    result = cv2.bitwise_and(frame, frame, mask=mask)
```

We finally show the result:

```python
    cv2.imshow("Frame", frame)
    cv2.imshow("Red", red)
    cv2.imshow("Blue", blue)
    cv2.imshow("Green", green)
    cv2.imshow("Result", result)
    key = cv2.waitKey(1)
    if key == 27:
        break
```

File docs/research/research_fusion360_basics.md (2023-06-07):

# How to get Fusion360

## How to install

First of all you need to log in using your HvA account. If you go to your account on the top right and click on it, you will get a dropdown menu. From the menu under the category account click on products and services. From there you should be able to download fusion360 among the available options. 

# The basics

Once you open Fusion360 you will be presented with the following screen. 
Fusion360StartScreen

First of all lets look at the bottom of the screen. You will see the following toolbar. 

Fusion360BottomBar

This toolbar is for controlling what your mouse does. For example the first option in the toolbar is the orbit tool. It lets you control the rotation of the project using your cursor. Another way to control the rotation of the project is using the rotation box on the top right. 

### Different model types
Next lets look at the top. 

Fusion360TopBar

First you will see solid, surface and mesh etc. 

The main basic ones are solid, surface, mesh and form. 

Solid and surface are both used to create normal basic shapes but the main difference is that solid objects are filled while surface objects are hollow.
Mesh is essentially any imported 3d material. For example importing someone else's project, it would then be put into the project as a mesh. 
Form is what is used to create weird objects with very curvy form, and it offers a lot of flexibility in its design. 
For more information on the different types of models you can watch the following video which goes more in depth. 

<iframe width="560" height="315" src="https://www.youtube.com/embed/DiBJt318VIc" title="YouTube video player" frameborder="0" allow="accelerometer; autoplay; clipboard-write; encrypted-media; gyroscope; picture-in-picture" allowfullscreen></iframe>

### Creating a basic object shape

Fusion360Create

Once you click on the create button you can choose a plane on which to place the object. 

Fusion360Planes

Now you can choose the size of the object you want to make. 

Fusion360ChooseSize

After you place the object you will get the following screen which is self-explanatory where you just have to move the arrows to the direction you want to expand the object to. 

Fusion360AdjustSize

This is how you can create basic objects in fusion360. 

For more information below is a beginner guide video that is pretty short but has a lot of information. 

<iframe width="560" height="315" src="https://www.youtube.com/embed/9Jgty4QDtss" title="YouTube video player" frameborder="0" allow="accelerometer; autoplay; clipboard-write; encrypted-media; gyroscope; picture-in-picture" allowfullscreen></iframe>

Below is another guide on how to make holes in fusion360. This could be useful later on. 

<iframe width="560" height="315" src="https://www.youtube.com/embed/4bDNXpWQaW4" title="YouTube video player" frameborder="0" allow="accelerometer; autoplay; clipboard-write; encrypted-media; gyroscope; picture-in-picture" allowfullscreen></iframe>

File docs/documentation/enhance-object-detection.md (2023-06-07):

# Enhancing the object detection

We noticed the Drawbot wasn't good enough at detecting shapes when we were using opencv. That is why we made the
decision to switch to machine learning and train our drawbot to detect the shapes ourselves.

We are using [Teachable Machine](https://teachablemachine.withgoogle.com/) to train our shape detection model. We added
around 1000 pictures for each shape. We devided the shapes into 4 categories, circles, rectangles, triangles and
nothing. shapes
Our model is now able to detect all 4 shapes pretty well.

circle example

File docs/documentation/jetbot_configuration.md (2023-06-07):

# Jetbot Configuration

## Hotspot configuration

To configure the hotspot, you should download the create_ap library from
this [link](https://github.com/oblique/create_ap).
Once it's downloaded, extract the files and start the terminal in the extracted file.
Now, we need to configure the SSID and the password of the hotspot, by editing the create_.ap.conf within the extracted
file.
Thereafter, execute the following commands in your terminal ```cd create_ap```  &#8594 ```make install```

To make the hotspot start on boot, execute this command:

``` bash 
systemctl enable create_ap
```

## Flask server on boot up

To configure a service on boot, we should firstly edit the following files:

1. rc-local.service
2. rc.local

First, we need to configure the rc.local as follows:
rc.local

And the rc-local.service as follows:
rc.local

Eventually, executing the following command to have the server up and running once the Jetbot is booted up:

```bash
sudo systemctl enable rc-local.service 
```

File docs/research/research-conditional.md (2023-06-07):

# What is conditional desgin? 

"Conditional Design is a design method formulated by the graphic designers Luna Maurer, Jonathan Puckey, Roel Wouters and the artist Edo Paulus, in which conditions and rules of play are drawn up that invite cooperation within a ‘regulated’ process towards an unpredictable design or result. The book Conditional Design sets out to provide insight into the method in an exciting way and to invite others to apply the method themselves. Conditional Design plays with chance, frameworks and generative systems and is a 'play' method that provides possibilities for every creative person. The system is surprisingly simple, and allows every team to set their own rules. The book functions as a workbook; the designer Julia Born has organized the material step-by-step, and shows in Conditional Design Workbook just how this exciting process works."(Conditional Design - Conditional Design Workbook, n.d.)
Cover of the conditional design book

So to put this in my own words, conditional design is about working together with rules and other people or robots? I think this book is very interesting for us to see what we can do with the Drawbot. If we can make the Drawbot react to certain colors and set rules for the player. The Drawbot and the player would be creating a unique design every time they play the game. 

## An example what a game of conditional desgin would look like
There a many more examples in the [Conditional design workbook](https://drive.google.com/file/d/1iAItmp1dUeC13vGlkwd-HNL-QiJKQt5D/view) but this one seemed the most fitting for the Drawbot.
Conditional design page 1
Conditional design page 2
Conditional design page 3
Conditional design page 4
Conditional design page 5
Conditional design page 6
Conditional design page 7
Conditional design page 8

### Resources for this research
[Conditional design website](https://conditionaldesign.org/)

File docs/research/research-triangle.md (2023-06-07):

# What can we draw when the drawbot detects a triangle?

As a first step I think it would be a good idea to draw a star out of a triangle. To make a star out of a triangle you just have to draw another triangle inside of the already existing one. Triangle star

The way our Drawbot should draw the triangle is displayed in the drawing below. Draw circle The dotted lines are displaying the lines the drawbot should draw. So it has to make 3 different  lines, start at the first red dot and move to the next one.

# How to draw a triangle with the drawbot

```python
from jetbot import Robot
import time
# Init the drawbot
drawbot = Robot()

INITIAL_SPEED = 0.6
LEAVE_CURVE_TIMEOUT = 0.3
TIMEOUT_TURN = 2.5
# First we let the drawbot draw a straight line
def drawTriangle(drawbot):
    SLOW_SPEED = INITIAL_SPEED * 0.6

    print(SLOW_SPEED)
    
    # Curve forward
    drawbot.forward(SLOW_SPEED)
    time.sleep(LEAVE_CURVE_TIMEOUT)

#     # Quick turn
    drawbot.set_motors(0, INITIAL_SPEED)
    time.sleep(LEAVE_CURVE_TIMEOUT)
    
    drawbot.set_motors(-INITIAL_SPEED, 0)
    time.sleep(LEAVE_CURVE_TIMEOUT)

#     # Curve forward
#     drawbot.forward(SLOW_SPEED)
#     time.sleep(LEAVE_CURVE_TIMEOUT)
    
    drawbot.stop()
```
For now we can draw a triangle with the drawbot, it's going to be pretty hard to draw the triangle on top of the other triangle to make a star. This is something we can try to do in future sprints.

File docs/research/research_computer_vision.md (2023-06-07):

# What is Computer Vision?

On this research page I will explain Computer Vision. First of all I will begin by explaining what Computer Vision is and how it is different from machine learning.

Computer Vision is a method a computer can use to gain high level understanding from digial images or videos. If a computer is set up to use Computer Vision it can understand and automate tasks that a human eye can do. Computer Vision tasks include methods for acquiring, processing, analyzing and understanding digital images. It can do this by extracting data from an image created by the camera in order to produce numerical or symbolic information. In the image below you can see what a computer using CV sees in an image.

CV elephant

With this information a computer can execute multiple tasks. Some of those tasks include recognition, motion analysis, scene reconstrution and image restoration. Your smartphone camera also uses Computer Vision to scan a QR-code.

The difference between CV and machine learning is that CV attemps to train computers to recognize patterns in visual data in a similair way humans do. On the other hand machine learning enables computers to learn how to process and react to data inputs based on criteria set by previous actions. Machine learning is more general and does not necessarily involve visual data.

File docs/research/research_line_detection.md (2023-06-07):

# Line detection in python with OpenCV

## How it works using Hough Transform 
The Hough Transform is a technique used in image processing to detect any shape that can be represented mathematically. It can detect the shape even if it is slightly broken or distorted.
Using the HoughLine transform method, we will see how the Hough transform works for line detection. To use the Houghline method, an edge detection of the specific image is required first. Read the article Edge detection for more information on the technique.

## Basics of Houghline Method
A line is represented as y = mx + c or, in parametric form, as r = xcos + ysin, where r is the perpendicular distance from the origin to the line and is the angle formed by this perpendicular line and horizontal axis measured in counter-clockwise rotation. (The direction depends on how the coordinate system is represented.) OpenCV makes use of this representation).



### The Houghline method in action
It first creates a 2D array or accumulator (to hold the values of two parameters), which is initially set to zero.
Let rows represent the r and columns represent the ()theta.
The size of the array is determined by the level of accuracy required. If you want the accuracy of angles to be one degree, you will need 180 columns (Maximum degree for a straight line is 180).
The maximum distance possible for r is the image's diagonal length. Using one pixel accuracy, the number of rows can be the image's diagonal length.

### code example 
```python
# Python program to illustrate HoughLine
# method for line detection
import cv2
import numpy as np
    def get_image_with_lines2(self, image_path):
        img = cv2.imread(image_path)
        gray = cv2.cvtColor(img, cv2.COLOR_BGR2GRAY)

        kernel_size = 5
        blur_gray = cv2.GaussianBlur(gray, (kernel_size, kernel_size), 0)
        low_threshold = 50
        high_threshold = 150
        edges = cv2.Canny(blur_gray, low_threshold, high_threshold)

        rho = 1  # distance resolution in pixels of the Hough grid
        theta = np.pi / 180  # angular resolution in radians of the Hough grid
        threshold = 15  # minimum number of votes (intersections in Hough grid cell)
        min_line_length = 50  # minimum number of pixels making up a line
        max_line_gap = 20  # maximum gap in pixels between connectable line segments
        line_image = np.copy(img) * 0  # creating a blank to draw lines on

        # Run Hough on edge detected image
        # Output "lines" is an array containing endpoints of detected line segments
        lines = cv2.HoughLinesP(edges, rho, theta, threshold, np.array([]),
                                min_line_length, max_line_gap)

        for line in lines:
            for x1, y1, x2, y2 in line:
                cv2.line(line_image, (x1, y1), (x2, y2), (255, 0, 0), 5)
        lines_edges = cv2.addWeighted(img, 0.8, line_image, 1, 0)

        return lines_edges
```

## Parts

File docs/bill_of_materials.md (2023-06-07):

Below you will find the Bill of Materials with the components used to create the pen holder attachment to the JetBot. If you have not yet made the Jetbot you can find the materials and instructions [here](https://jetbot.org/master/bill_of_materials.html). JetBotV1 is the version without a moving pen. You can find the V3 and also latest version below.

## Bill of Materials DrawBot V1

| <b>Part</b>                  	| <b>Quantity</b> 	| <b>Cost</b>  	| <b>URL</b>	                | <b>Notes</b>        	               |
|                               |----------	        |-------	    |	                            |	                                  |
| Pen holder attachment 	    | 1 	            | --            | [STL](../files/PenHolderV1.stl) | See [Pen holder attachment](https://iot.dev.hihva.nl/2022-2023-sep-jan/group-project/vitalityandaging-drawing-together/documentation/pen_holder_doc/) 	|
| Screw wedge           	    | 1             	|--          	| [STL](../files/Screw_Wedge.stl) | See [Pen holder attachment](https://iot.dev.hihva.nl/2022-2023-sep-jan/group-project/vitalityandaging-drawing-together/documentation/pen_holder_doc/) 	|
| Screw M2x10               	| 14       	        | €2,27 	    | [AliExpress](https://nl.aliexpress.com/item/1005001627481386.html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)|                         	|
| Screw M2x20                	| 4        	        | €3,48 	    | [AliExpress](https://nl.aliexpress.com/item/1005003652695473.html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) 	|                             |
| Bolt M5x30            	    | 1              	| N.A   	    | Any with these specifications| Length depends on what type of pen you want to hold. 30mm holds any pen/pencil|

### Final result
This is what the finished Drawbot is going to look like.

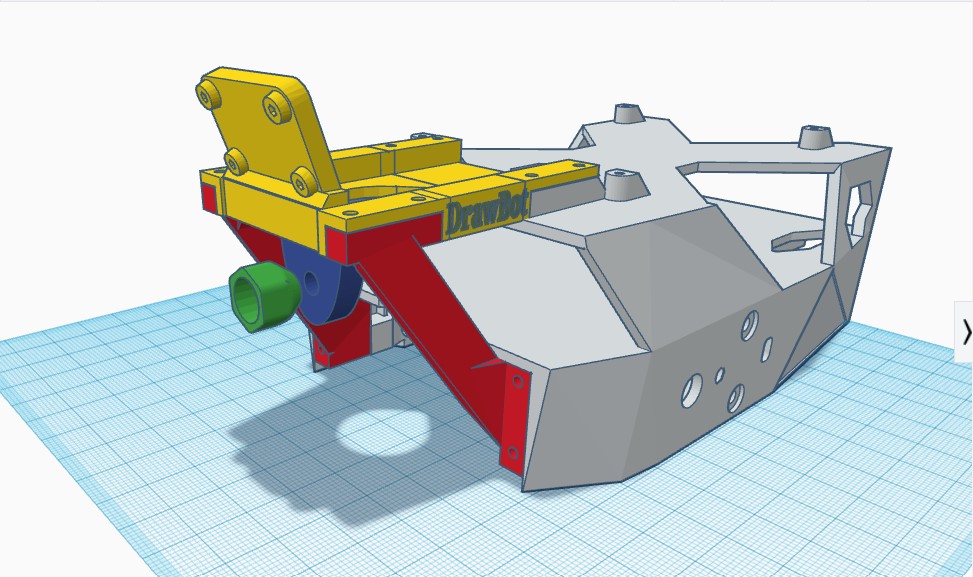
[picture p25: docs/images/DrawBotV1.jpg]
Finished Drawbot


## Bill of Materials DrawBot V3
There is no BOM of the V2 Becaue those changes were insignificant

| Part 	| Quantity 	| Cost 	| URL | Notes |
|---	|---	|---	|---|---	|
| Pen holder attachment 	| 1 	| -- | [STL](../files/DrawBotV3.stl) | See [Pen holder attachment](https://iot.dev.hihva.nl/2022-2023-sep-jan/group-project/vitalityandaging-drawing-together/documentation/pen_holder_doc/) |
| Bolt M6x40 	| 2 	| €3,49 (for a pack of 10)  | [Karwei](https://www.karwei.nl/assortiment/karwei-zeskantbout-voldraad-6x40-mm-10-stuks/p/B450662) 	| 
| Screw M2x10 	| 8 	| €2,27 	| [AliExpress](https://nl.aliexpress.com/item/1005001627481386.html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)	| 	|
| Screw M2x20 	| 4 	| €3,48 	| [Aliexpress](https://nl.aliexpress.com/item/1005003652695473.html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) 	| 	|
| Bolt M5x20 	| 1 	| €2,89 (for a pack of 15) 	| [Karwei](https://www.karwei.nl/assortiment/karwei-inbusbout-5x20-mm-15-stuks/p/B450598) | Length depends on what type of pen you want to hold. 20mm holds only markers. 30mm holds any pen or pencil 	|
| Bolt and nut M3x40 	| 1 	| €1,89 (for a pack of 15) 	| [Karwei](https://www.karwei.nl/assortiment/karwei-metaalbout-3x40-mm-15-stuks/p/B450633) 	| 	|
| WeMos D1 Mini ESP8266 	| 1 	| €7,00 	| [TinyTronics](https://www.tinytronics.nl/shop/nl/development-boards/microcontroller-boards/met-wi-fi/wemos-d1-mini-v4-esp8266-ch340) 	| 	|
| SG90 Mini Servo 	| 1 	| €3,25 	| [TinyTronics](https://www.tinytronics.nl/shop/nl/mechanica-en-actuatoren/motoren/servomotoren/sg90-mini-servo) 	| 	|
| DuPont Jumper wire Female-Female 	| 2 	| €0,50 	| [TinyTronics](https://www.tinytronics.nl/shop/nl/kabels-en-connectoren/kabels-en-adapters/prototyping-draden/dupont-compatible-en-jumper/dupont-jumper-draad-female-female-10cm-10-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) 	| 	|

You don't have to order the bolts and screws from the link just as long as they are the right size.

### Final Result
Below are some pictures of how the final product is going to look like.

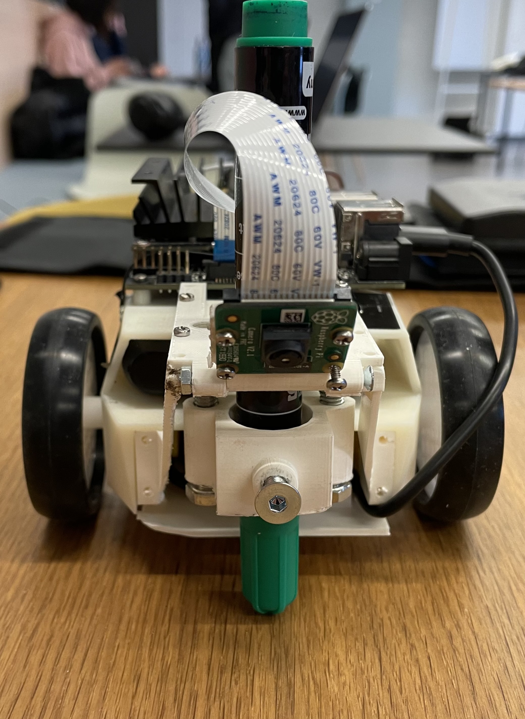
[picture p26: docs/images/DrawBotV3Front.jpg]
DrawBotV3Front

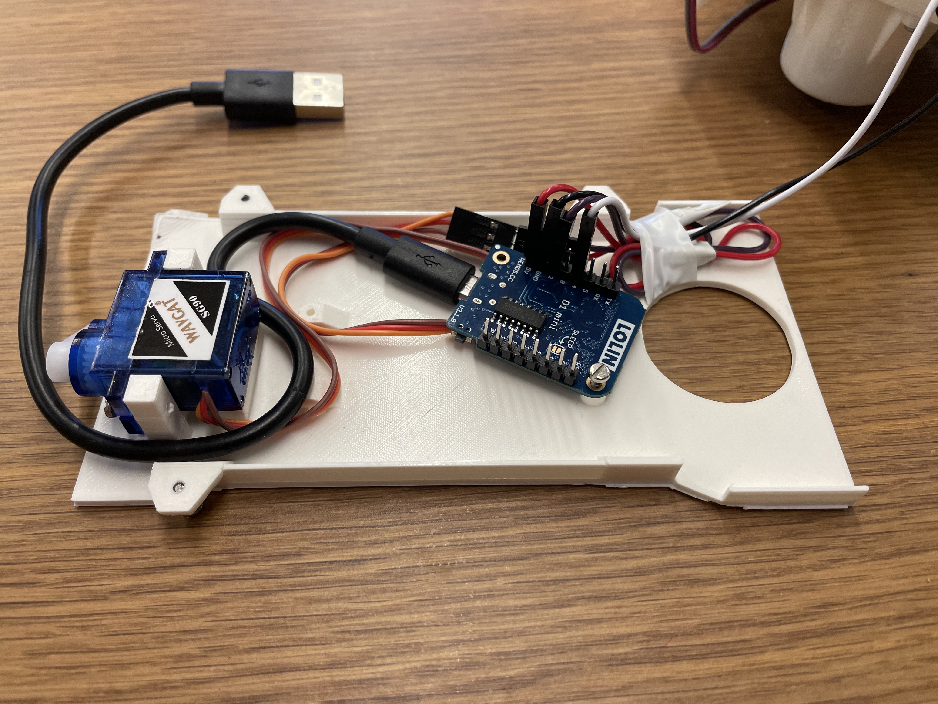
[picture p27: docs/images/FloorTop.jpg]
FloorTop


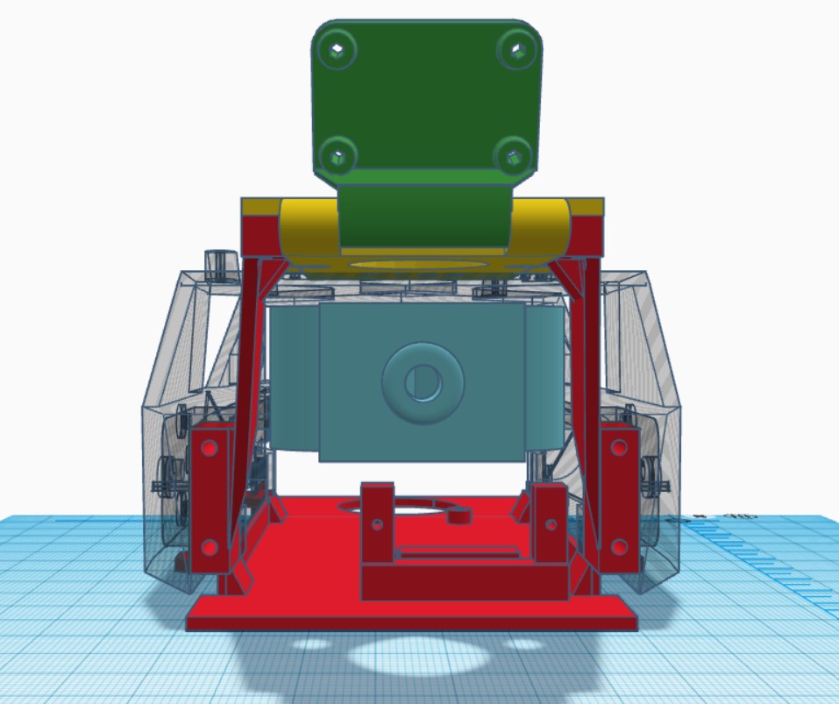
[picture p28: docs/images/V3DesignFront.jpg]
DesignFront

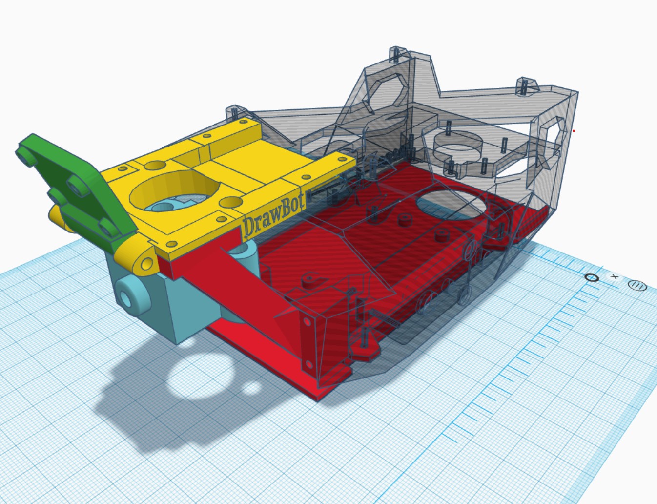
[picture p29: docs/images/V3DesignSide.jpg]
DesignSide


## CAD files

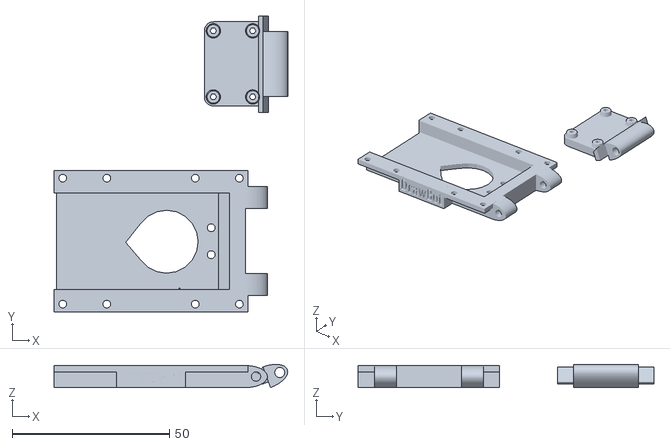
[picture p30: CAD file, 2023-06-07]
physical-design/drawbot_foldable_camera/Drawbot_foldable_camera.stl
74.2 x 94.0 x 7.35

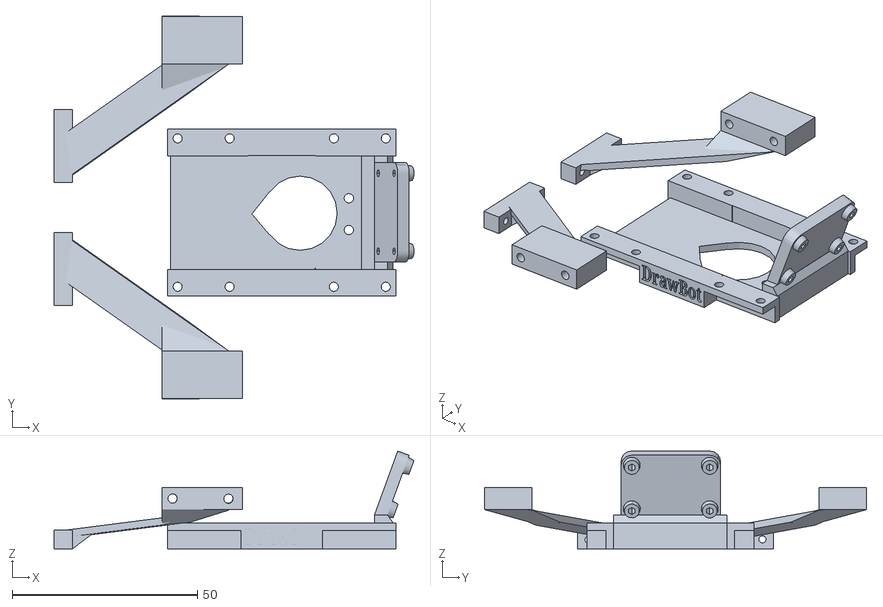
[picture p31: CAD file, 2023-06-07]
docs/files/PenHolderV1.stl
97.0 x 103.1 x 26.4

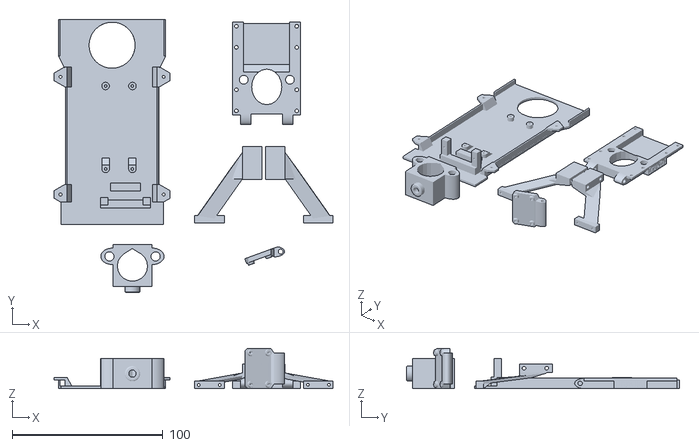
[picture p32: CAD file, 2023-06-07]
docs/files/DrawBotV3.stl
185.0 x 181.0 x 26.8

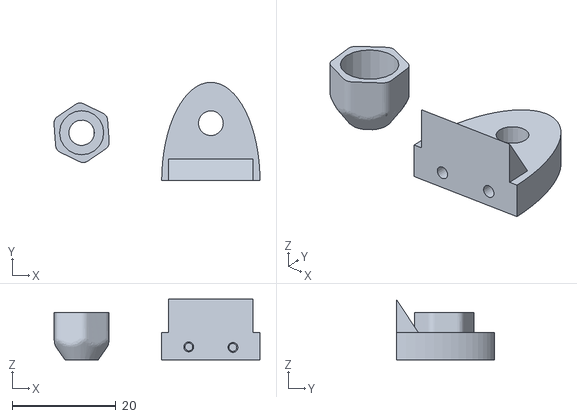
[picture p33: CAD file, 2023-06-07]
docs/files/Screw_Wedge.stl
39.8 x 19.0 x 11.7

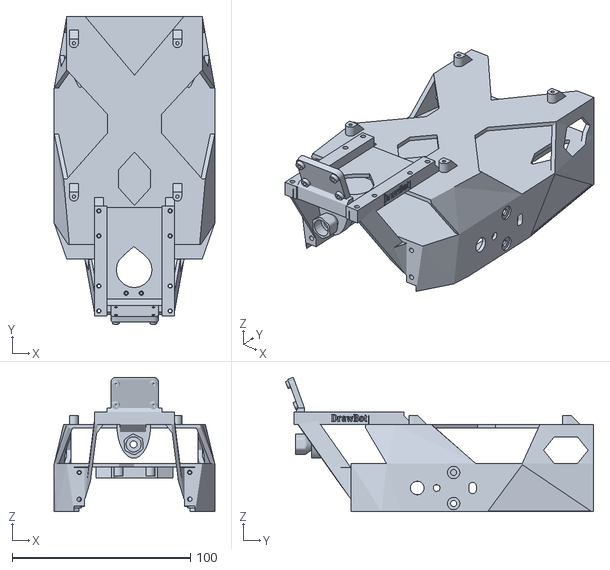
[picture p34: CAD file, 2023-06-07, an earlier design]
docs/files/DrawBotV1.stl
90.0 x 172.7 x 75.4

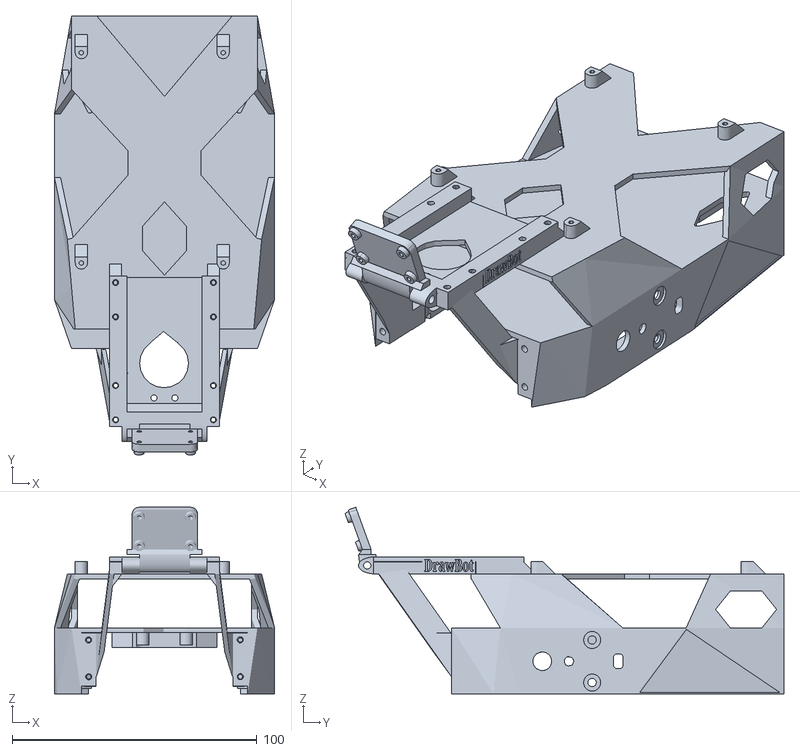
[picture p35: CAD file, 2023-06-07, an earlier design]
docs/files/DrawBotV2.stl
90.0 x 179.5 x 76.3

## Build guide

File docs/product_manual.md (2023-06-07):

# Assembly Guide

In this chapter there will be instructons on how to put the DrawBot together. Once you have reached this chapter you should already have all the items from the bill of materials including the items necessary to construct the JetBot (You can see how to put the JetBot together [here](https://jetbot.org/master/hardware_setup.html)). If you're interested in how we came up with the design you can go to the [pen holder attachment](documentation/pen_holder_doc.md) and [pen location research](research/research_pen_location.md) pages.

You will need some tools to make the Drawbot. These are a **screwdriver**, a **tap set** with M5 and M6 bits and a **soldering iron**.

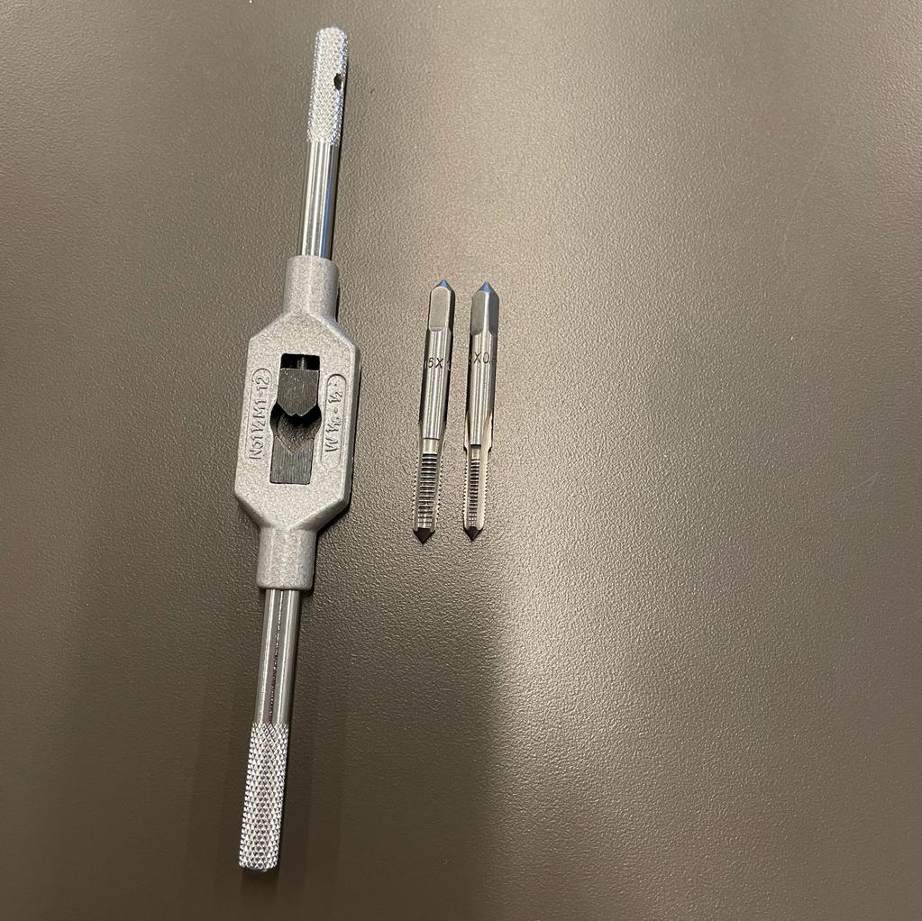
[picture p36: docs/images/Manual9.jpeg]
Tap bits


### Step 1 - Clean printed parts
Once you have printed all the parts for the DrawBot and created the JetBot you can start by cleaning the supports off of all the parts. Be careful with some areas as they are sometimes thinner than the supports and will easily break. 

3D printed parts are always a challenge due to the fact that not all printers have the same amount of accuracy and quality. You may need to adjust some parts to make them fit. This can be easily done by using sandpaper, a file or some clippers.

### Step 2 - Attach camera mount to JetBot

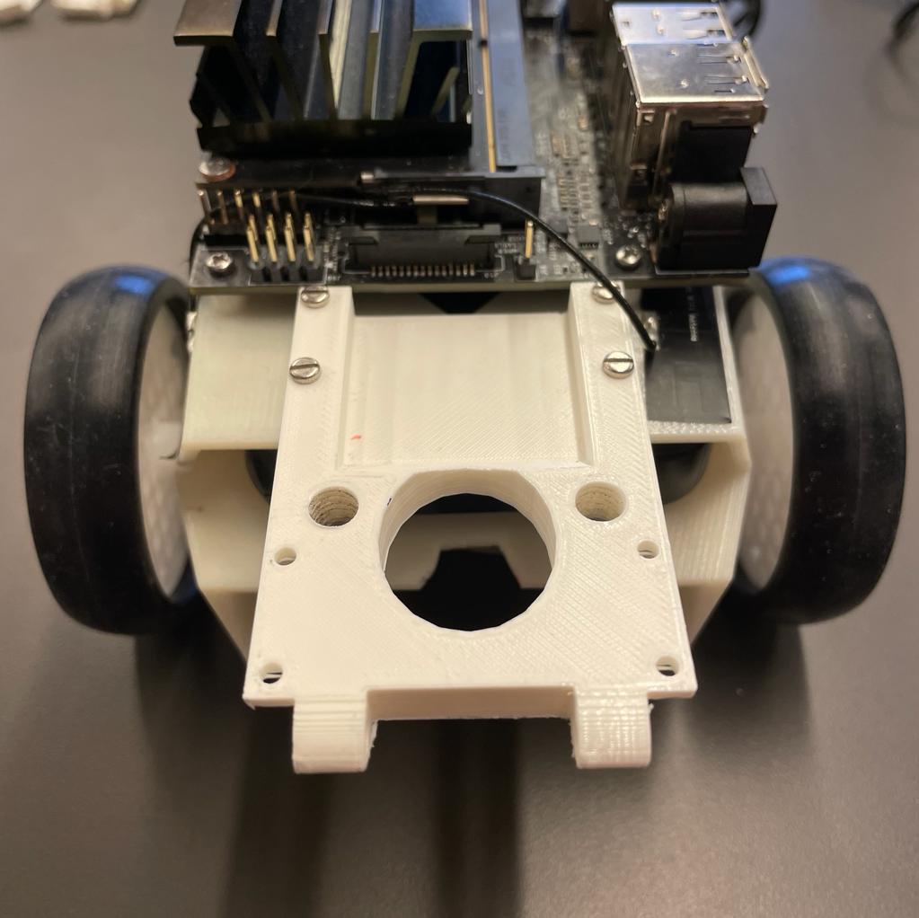
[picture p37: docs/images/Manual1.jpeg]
Camera Extension
 
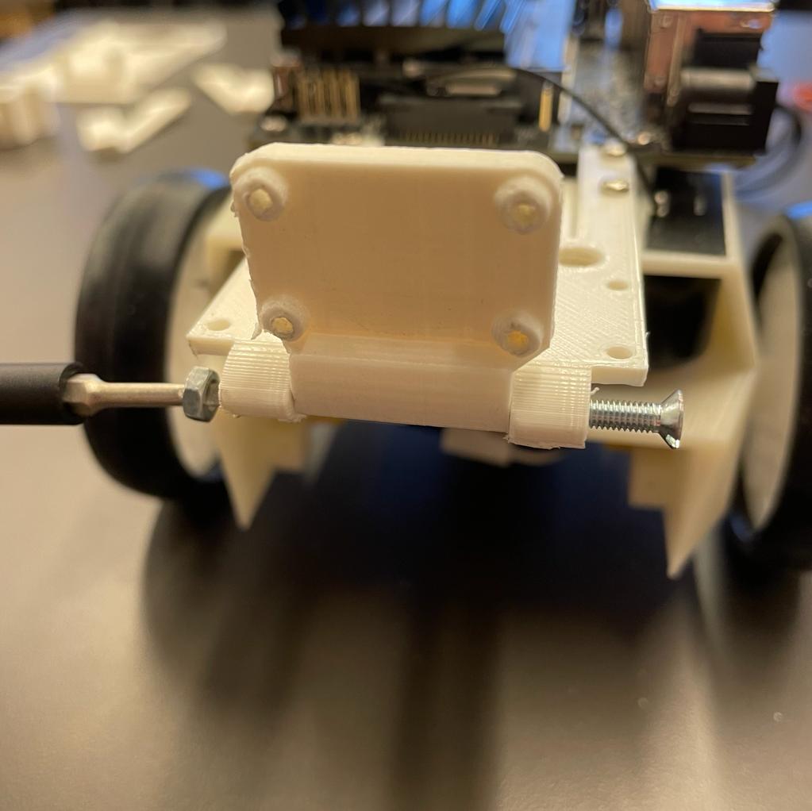
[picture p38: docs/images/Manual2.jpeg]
Camera Mount

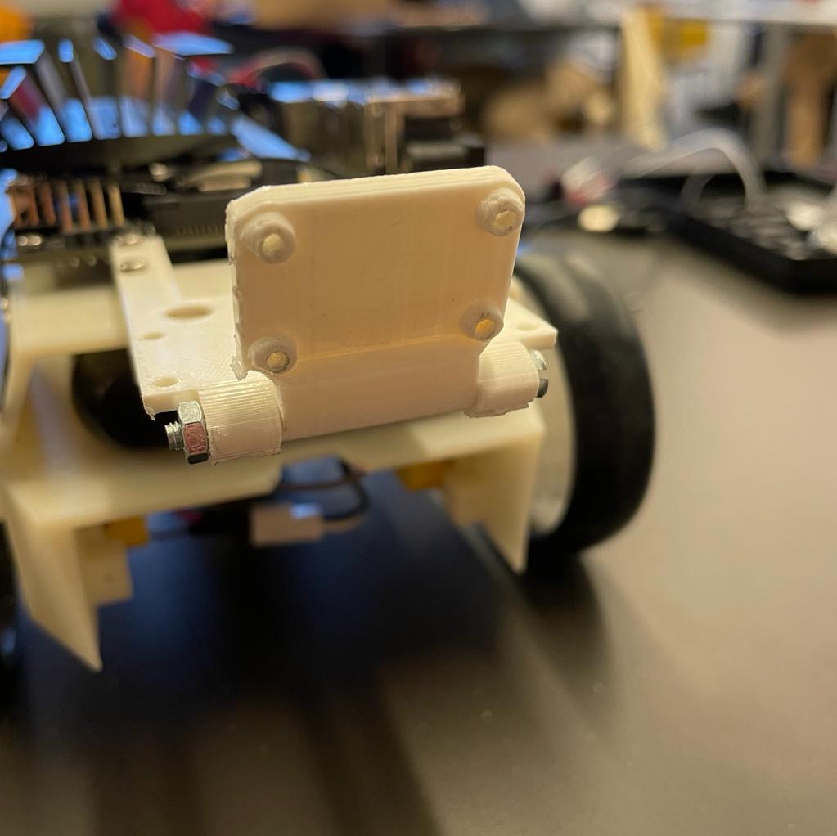
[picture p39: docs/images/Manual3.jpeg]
Camera Mount 2

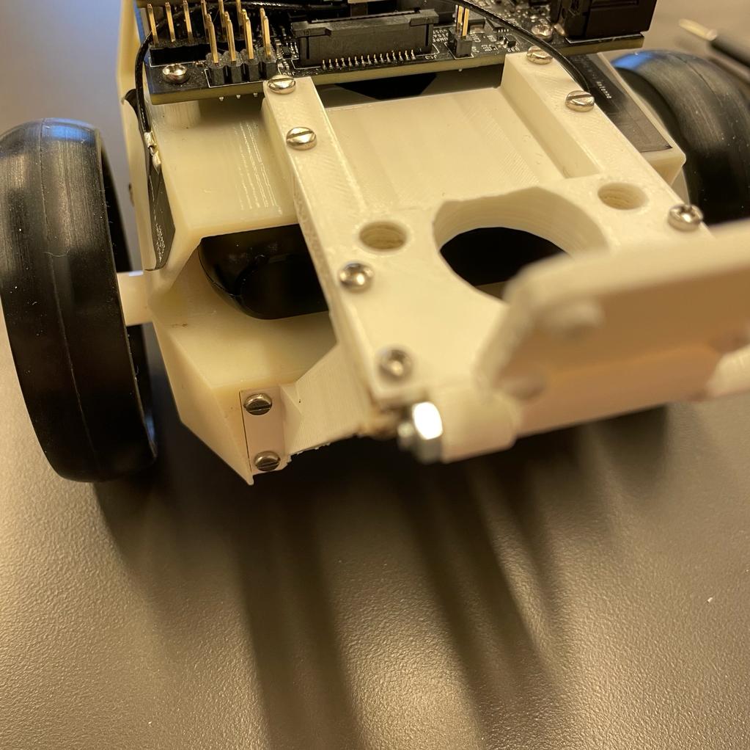
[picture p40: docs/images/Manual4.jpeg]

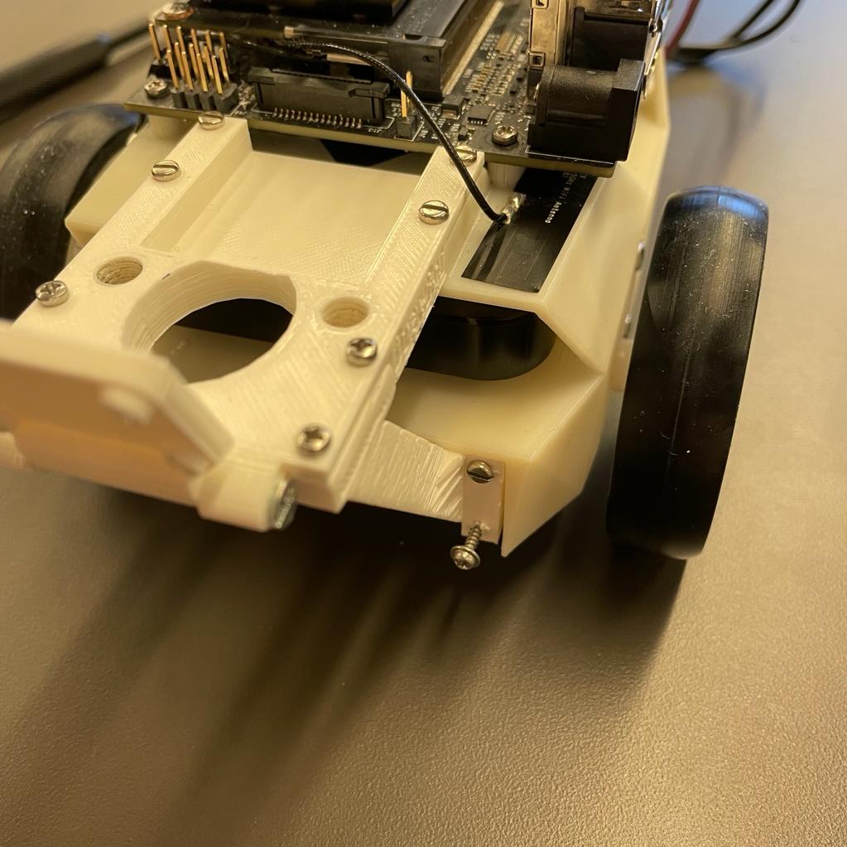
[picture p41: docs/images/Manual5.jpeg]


1. Mount the camera extension to the JetBot using 4 screws   

2. Attach the camera mount to the extension using the M3x40 bolt and nut

3. Attach the 2 diagonal supports to the camera extension using 4 M2x10 screws and to the JetBot using 4 M2x20 screws

### Step 3 - Mount Pen Holder

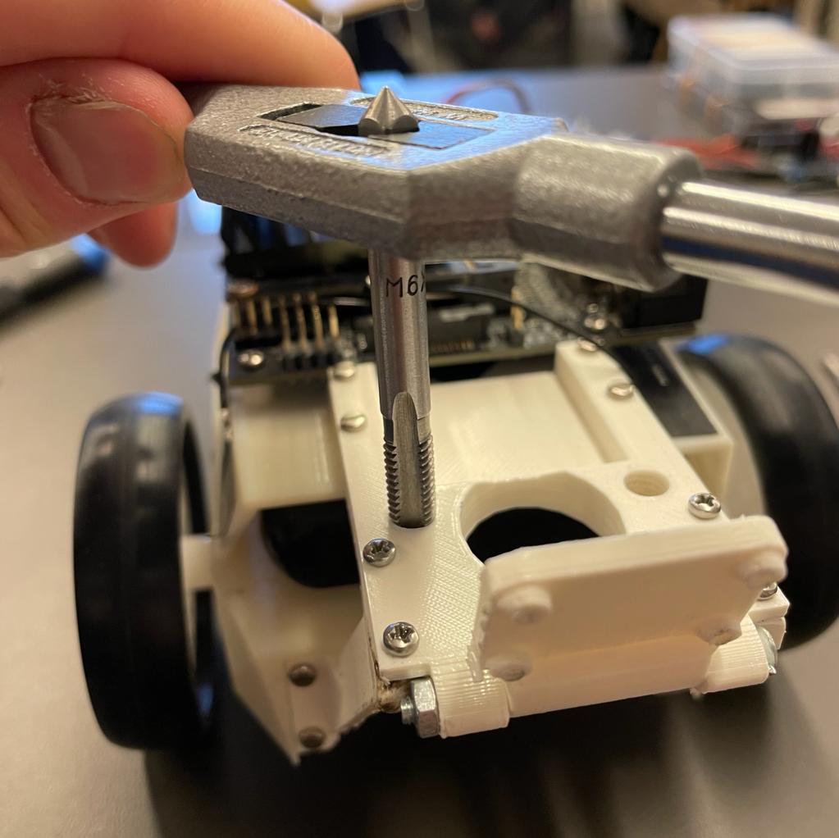
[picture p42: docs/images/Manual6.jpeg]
Hole tap left

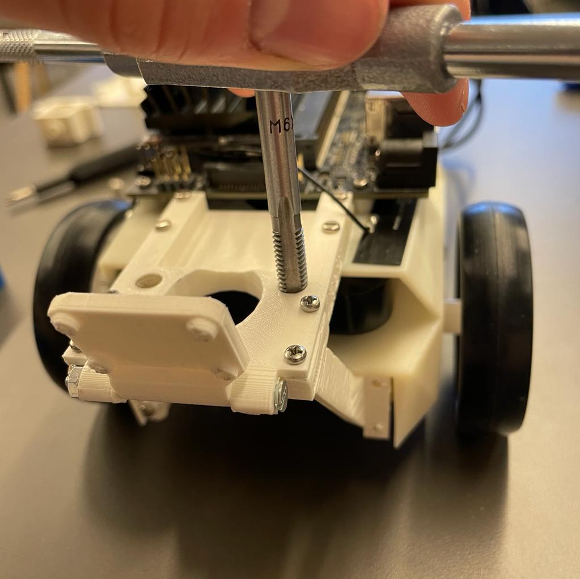
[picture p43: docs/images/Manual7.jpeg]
Hole tap right

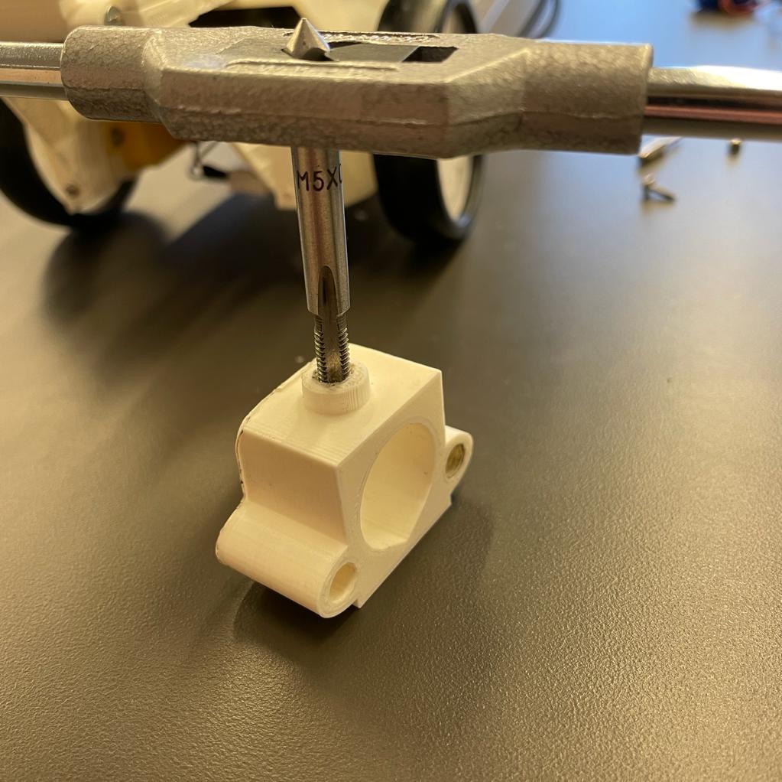
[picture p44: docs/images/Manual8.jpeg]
Tap pen holder

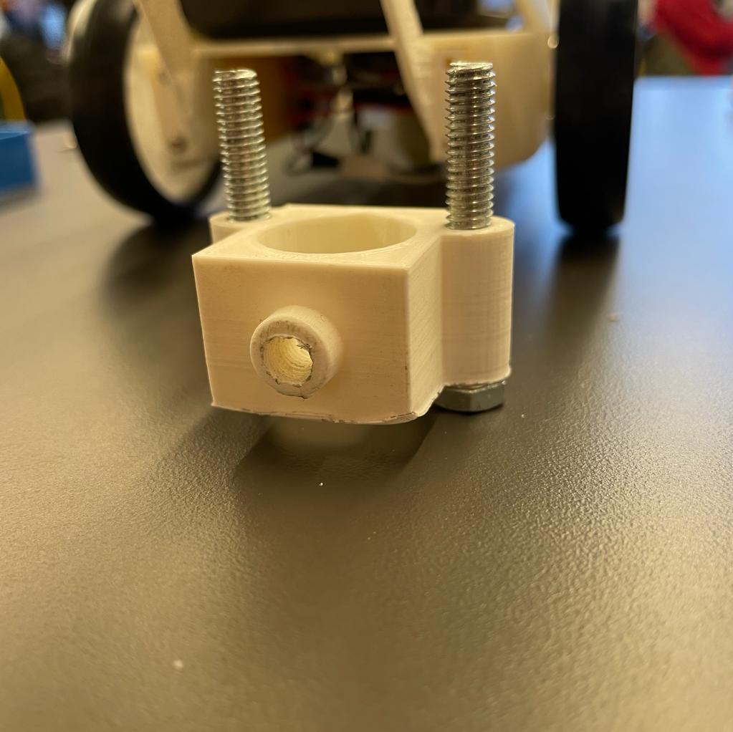
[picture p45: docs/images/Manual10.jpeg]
feed bolts

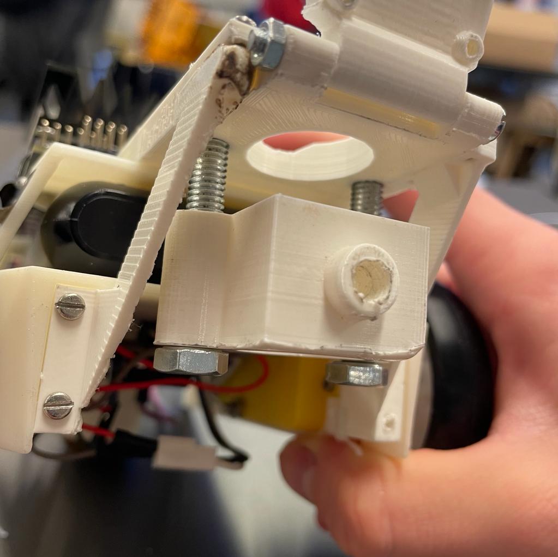
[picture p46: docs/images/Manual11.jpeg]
Attach holder

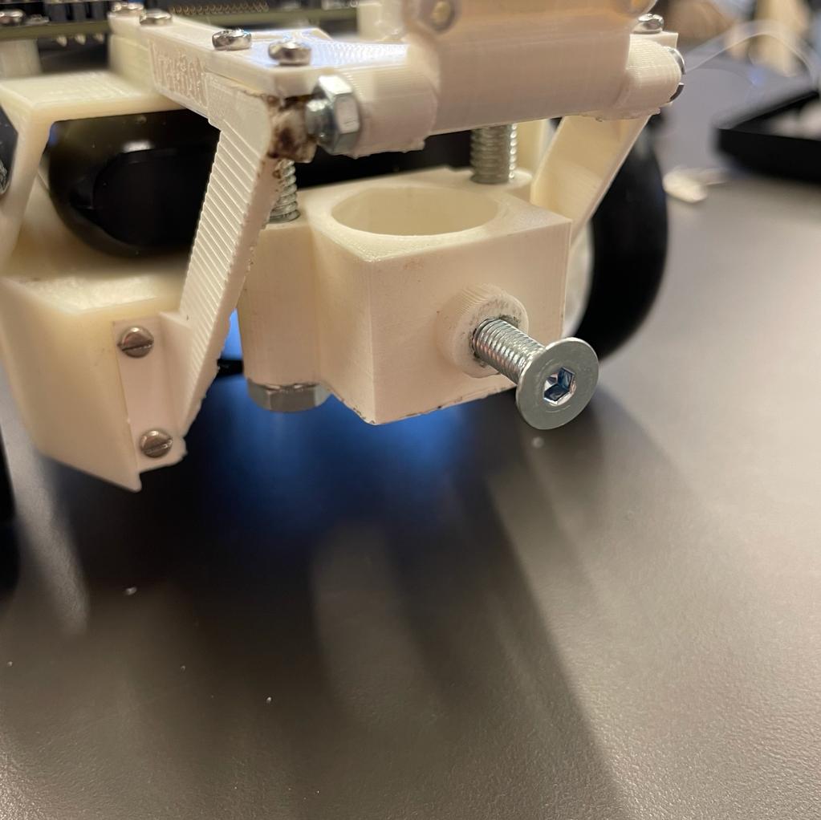
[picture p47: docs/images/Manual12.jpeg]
Attach screw


4. Attach the pen holder to the camera extension by first tapping the two holes in the camera extension with an M6 bit. 
5. Next tap the hole in the front of the pen holder with an M5 bit
6. To attach the holder to the extension feed the 2 M6x40 bolts through the pen holder and screw them in the camera extension from underneath

    !!! warning
        The holes of the pen holder might be too small for the bolt: To overcome this roll up a piece of sandpaper and feed it through the holes several times. This should be enough to make the holes slightly bigger.

7. Screw the M5x20 bolt into the front hole of the holder
8. Attach the camera to the mount with 4 M2x10 screws and put a pen in the holder and you are all finished!

<p align="center">
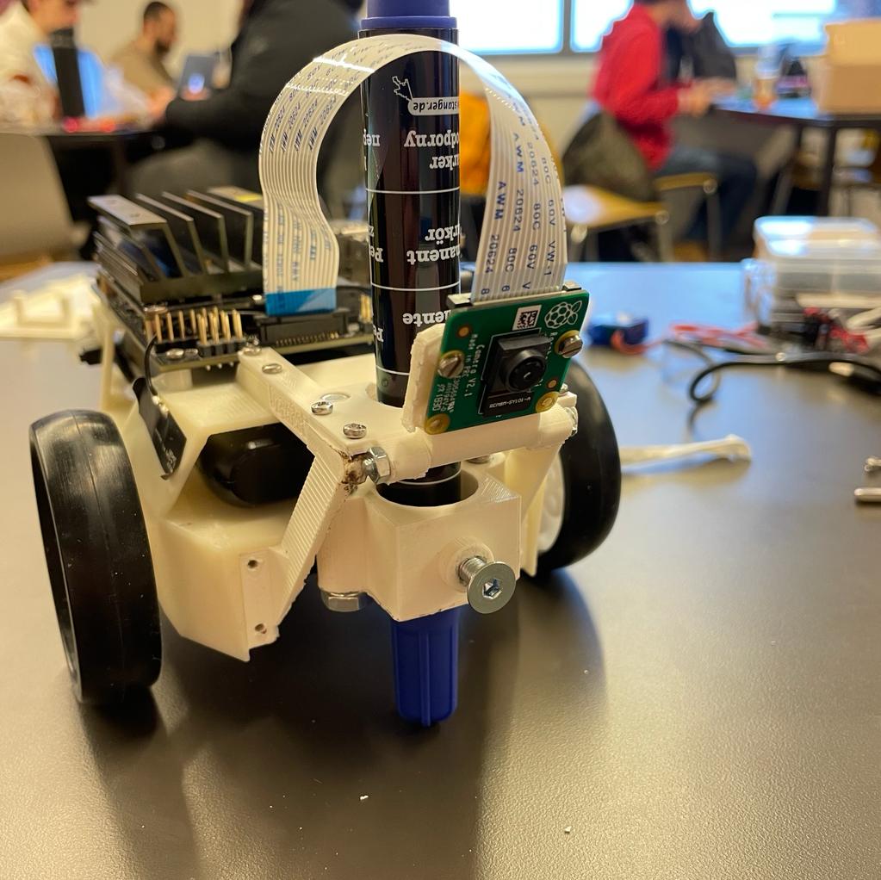
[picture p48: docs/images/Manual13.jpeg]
  
</p>

### Step 4 - Assemble the floor

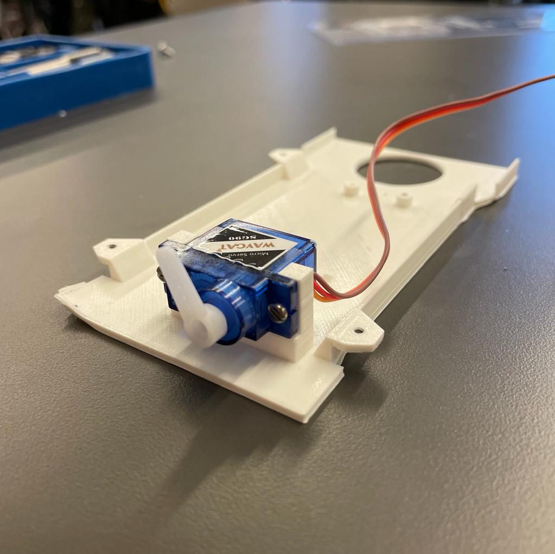
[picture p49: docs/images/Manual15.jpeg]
Attach Servo

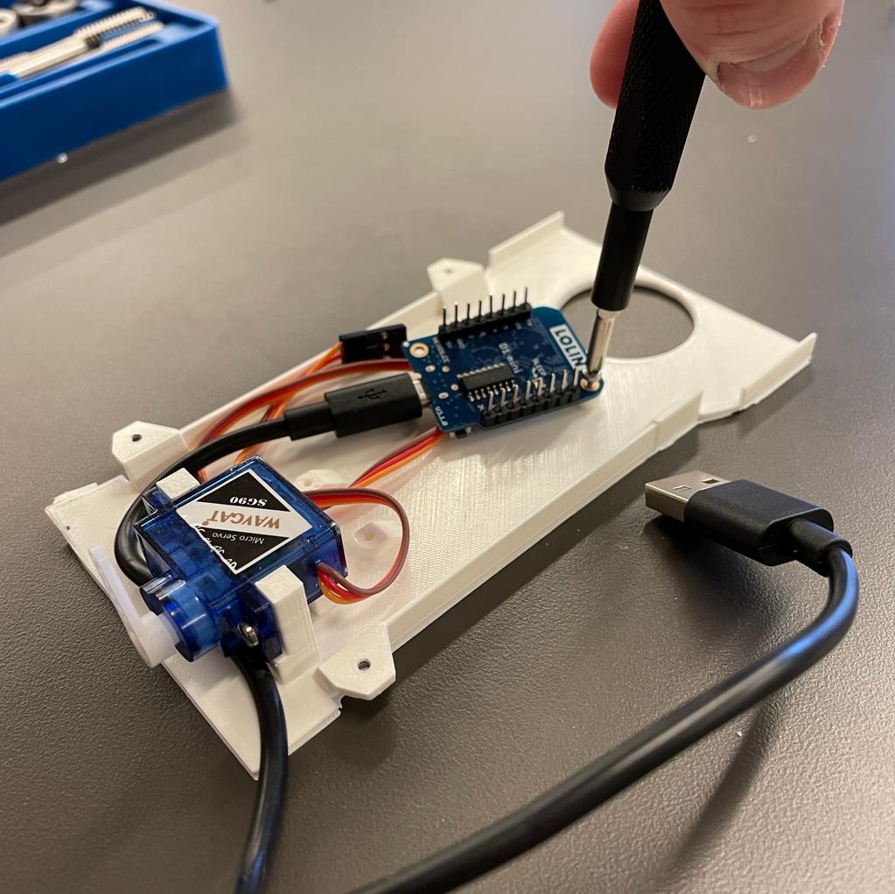
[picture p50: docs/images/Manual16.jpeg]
Attach WeMos

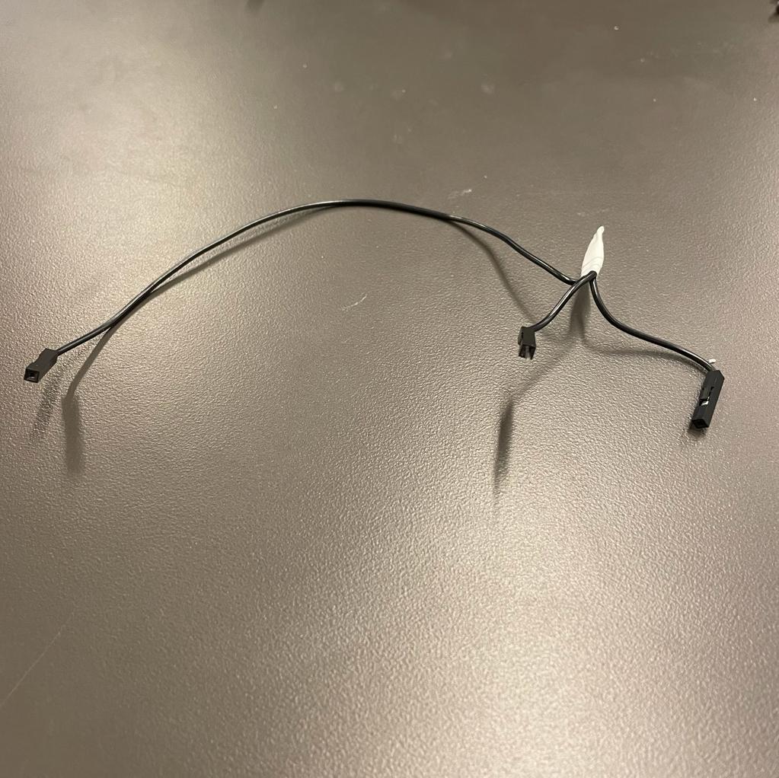
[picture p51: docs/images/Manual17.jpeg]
Soldered wire

<p align="center">
  
</p>

1. Attach the servo to the floor with 2 M2x10 screws. Make sure the servo has a far enough reach to point at least 135 degrees up.
2. Mount the WeMos using one or two M2x10 screws (depends on the kind of Wemos you have).
3. Follow the instructions in the wiring diagram above to connect these components to the Jetson Nano. 
4. You also need to solder the ground wire like in the image above so that it can connect on 2 pins and in the plug to the servo.
5. Finally attach the floor to the JetBot using 4 M2x10 screws

6. When the floor is done it should look like this

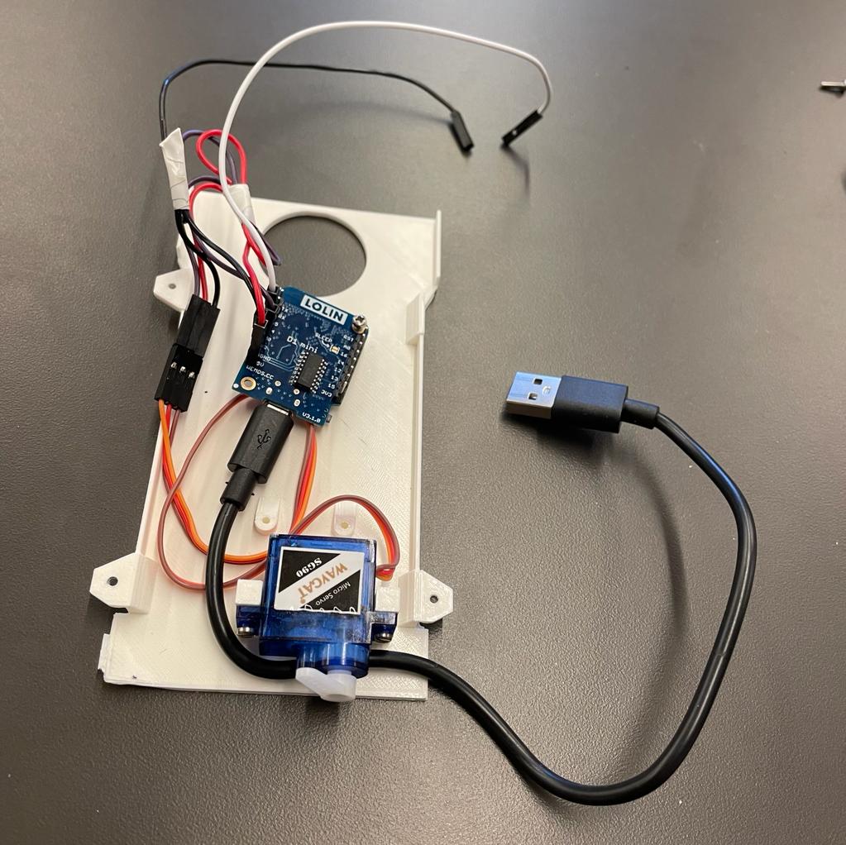
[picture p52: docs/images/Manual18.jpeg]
Finished Floor
    
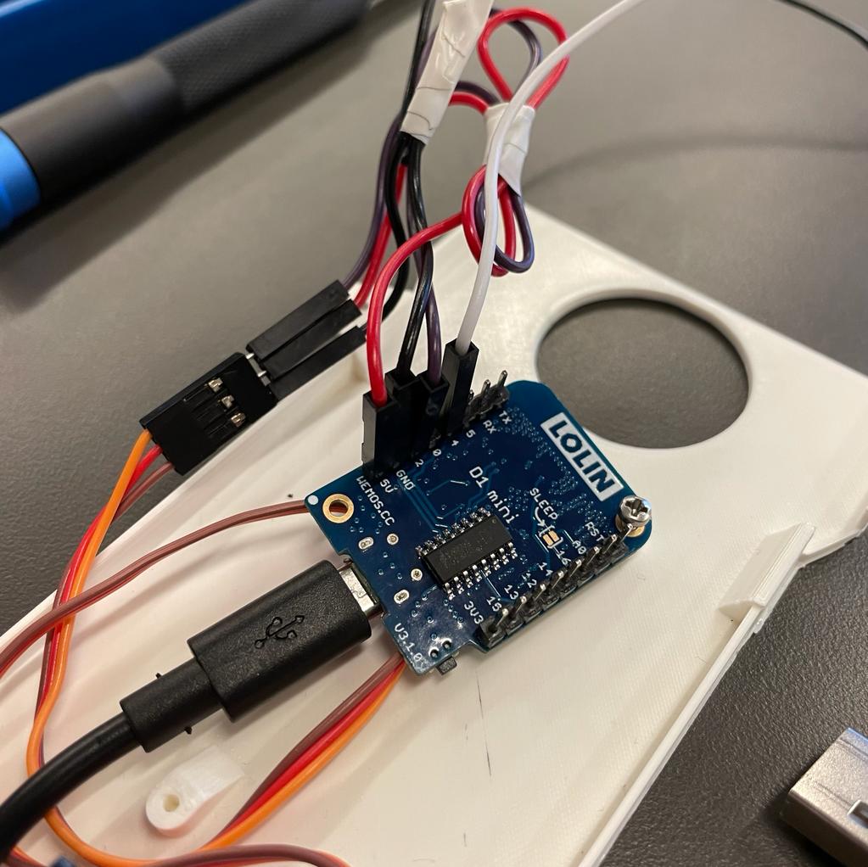
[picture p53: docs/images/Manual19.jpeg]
Finished Floor2
    

To finish up follow the wiring diagram to attach the two jump wires and plug the usb cable in one of the ports.

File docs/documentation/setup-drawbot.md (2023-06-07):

# How to clean install the Jetson Nano board

For this guide I followed the [setup documentation](https://developer.nvidia.com/embedded/learn/get-started-jetson-nano-devkit#intro) from Nvidia. 

1. We start off with downloading the [Jetson Nano SD card image](https://developer.nvidia.com/jetson-nano-sd-card-image).
2. We have to write the image to the sd card, we are going to use [Etcher](https://www.balena.io/etcher/) for that.
3. Plug the SD into the Jetson and connect it with your computer. 
4. After that you're going to open up the terminal and start the installation process follow the step on the [setup documentation](https://developer.nvidia.com/embedded/learn/get-started-jetson-nano-devkit#intro) from Nvidia. 

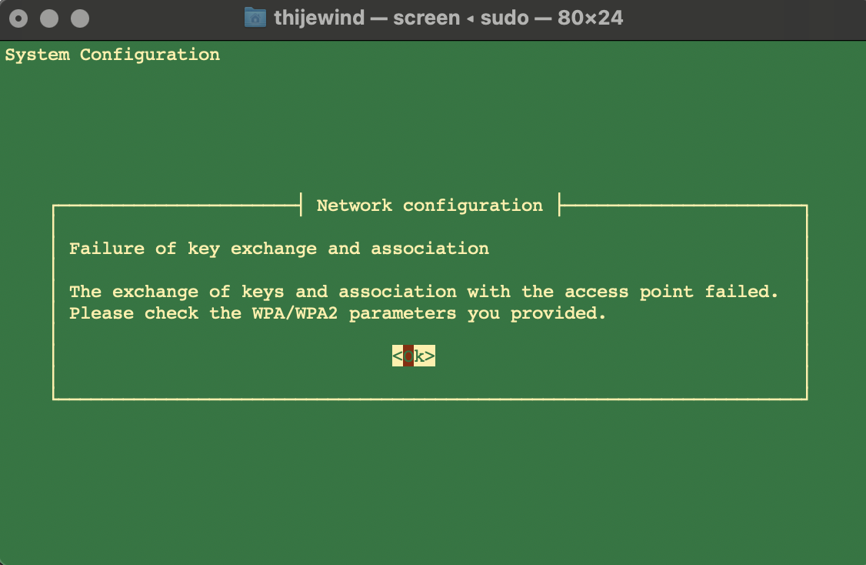
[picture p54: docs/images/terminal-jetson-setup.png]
Jetson setup error
I got stuck at the network configuration and couldn't get it to work. The Jetbot just kept giving error messages. 

After trying for like 3 times I decided I was going to use the other installation method. The setup with a display atteched to the Jetson Nano. This makes the installation process a bit easier since you don't have to do everything from the terminal. 
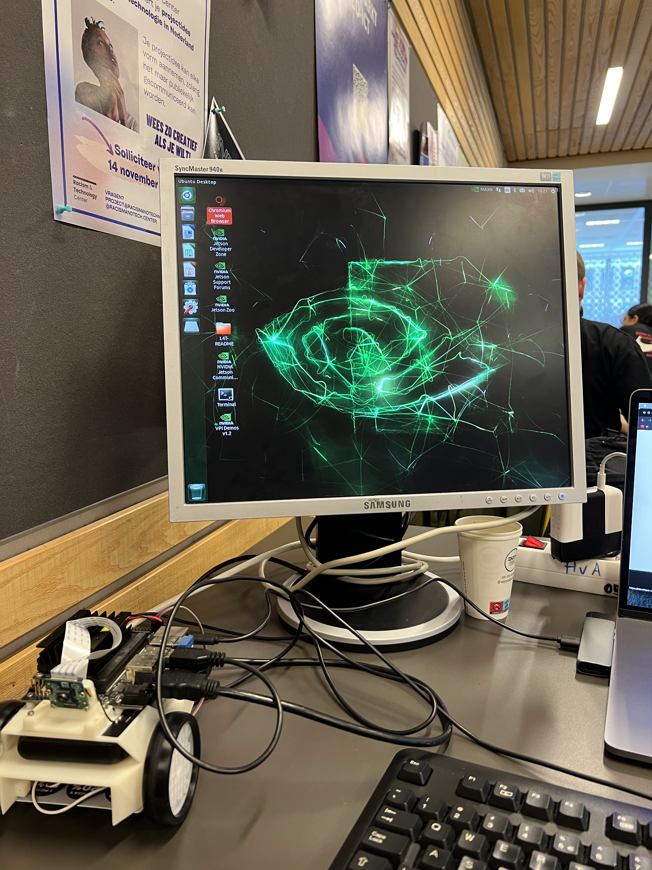
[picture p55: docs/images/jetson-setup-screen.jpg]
Jetson setup with sceeen


The Jetbot is working!

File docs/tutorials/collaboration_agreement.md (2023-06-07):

# Collaboration Agreement
 
[Collaboration Agreement](pdf/Collaboration%20Agreement.pdf)

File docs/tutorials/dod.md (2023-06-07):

# Definition of Done
The Definition of Done is an agreed-upon set of items that must be completed before a project or user story can be considered complete. It is applied consistently and serves as an official gate separating things from being “in progress” to “done.”

1. Code is deployed to the develop branch.
2. Code is peer-reviewed.
3. Documentation is updated.

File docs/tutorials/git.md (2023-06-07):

# Git Tutorial

## 1. Start working

When you start your day coding, you want to pull the incoming changes

```bash
git pull
```

## 2. Commit your changes

Once you've made some changes that work, you want to commit these changes so that they exist in the git log

```bash
# Stage the changes
git add .

# Commit the changes to the current branch
git commit -m "[YOUR-COMMIT-NAME-HERE]"
```

## 3. Push changes to GitLab

```bash
# Pull incoming changes
git pull

# Push changes
git push
```

## 4. Working on a new feature

Whenever you are going to work on a new feature or a new scrum card, you want to create a new feature branch.

First, make sure you are working on the 'develop' branch

```bash
# Switch to 'develop' branch
git checkout develop

# Pull the incoming changes from 'develop'
git pull

# Now make a feature.md branch based on 'develop'. 
# Make sure the name includes the: '/feature.md' annotation
git checkout -b "[YOUR-BRANCH-NAME]"

# Lastly, you'll want to send your feature.md branch to the server
git push --set-upstream origin "[YOUR-BRANCH-NAME]"
```

## 5. Merging my feature branch with GitLab

Done working on a feature? Here's what you do. While on the feature branch:

1. [Commit your changes](#2-commit-your-changes)

2. Update the branch with the incoming changes from 'develop'
```bash
git pull develop
```

3. Got a merge conflict? Follow [these steps](#6-resolving-merge-conflicts). Proceed to step 4

4. Go to GitLab -> 'Merge requests' and click on 'Create merge request'
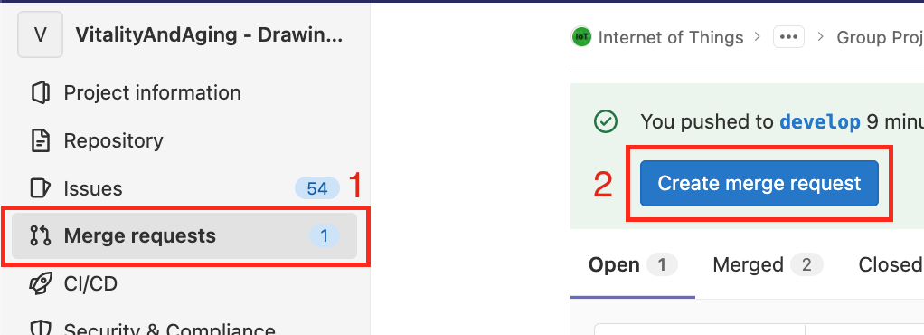
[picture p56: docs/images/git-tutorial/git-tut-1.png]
Create merge request screenshot


5. Make sure your are merging to the correct branch, which is 'develop'.
Button change branches
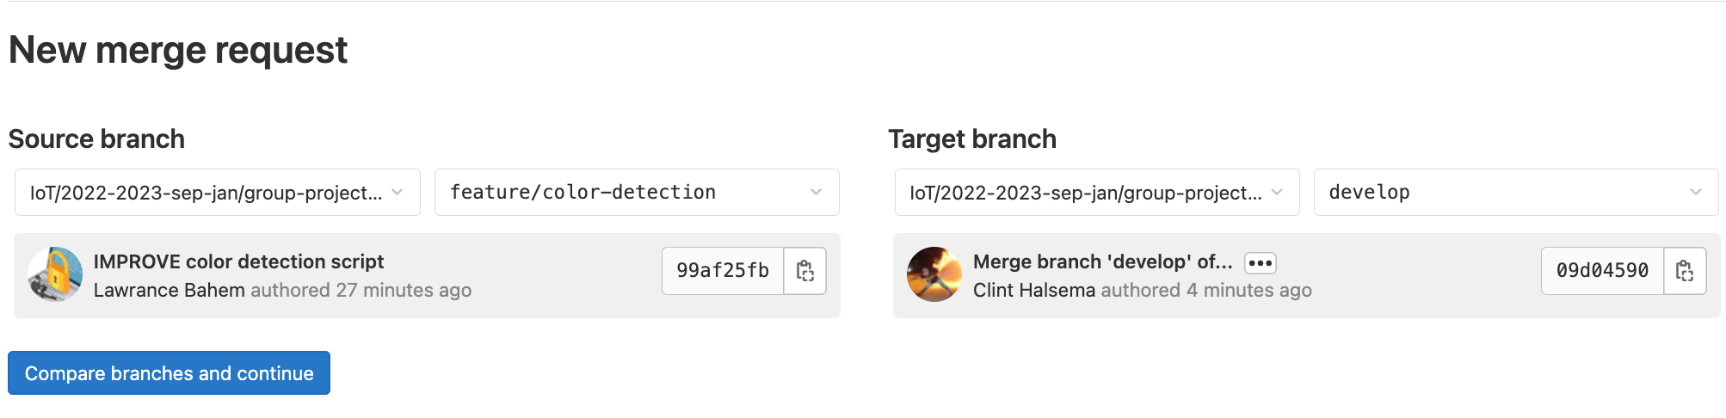
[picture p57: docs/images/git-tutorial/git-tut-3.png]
Select correct branch


Correct? Click: Compare branches and continue

6. Insert a suitable title

7. In the description, you'll find the definition of done. Check if your feature meets the definition of done requirements. If they do, tick them off using '- [x]'

7. Assign a reviewer. This person has to accept your merge request for it to be merged.

8. You can add a Milestone if neccesary

9. Click: 'Create merge request'

## 6. Resolving merge conflicts

If you've pulled the 'develop' branch into your feature branch, it is possible you'll get a merge conflict.
Follow the next instructions to resolve this.

1. Within VSCode, go to the file containing the conflict.

You'll see something similar to the screenshot below:
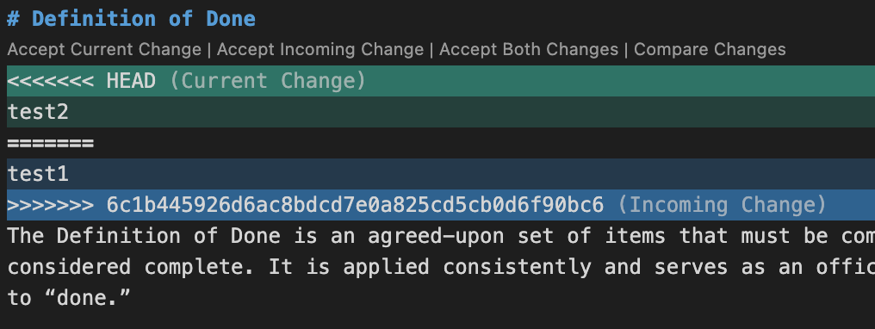
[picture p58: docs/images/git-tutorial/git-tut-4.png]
merge conflict vscode


2. Solve the conflicts, then commit the Merge commit to the feature branch.

3. Now make the merge request using [these steps](#5-merging-my-feature-branch-with-gitlab)

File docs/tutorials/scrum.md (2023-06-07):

# Scrum tutorial

On this page you can find how we make use of the scrum boards.

## 1. Create a new issue
#### Add a new issue/user story
When you have a new idea or function you want to add to the project you can create a new card in the <b>"product backlog"</b>. To get here you click on the <b>Issues > List > New Issue</b> on the top right of the screen.

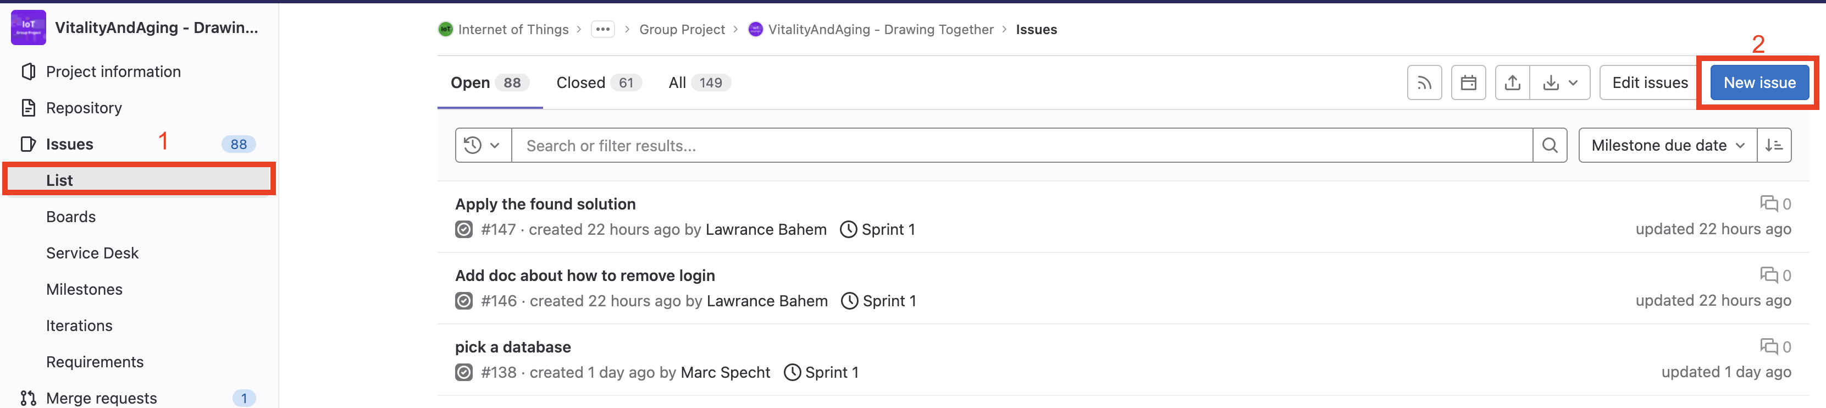
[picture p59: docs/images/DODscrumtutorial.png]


After that you can define whether it is a research or a feature card. 

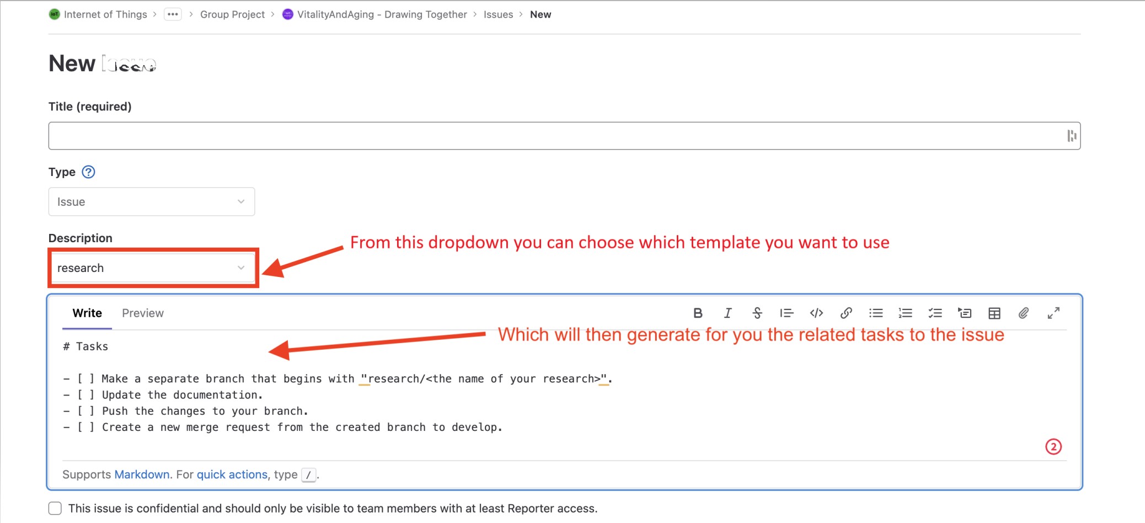
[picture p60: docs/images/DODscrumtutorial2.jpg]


You need to make this into a user story which means start with "as a user I want to" or "as a developer I want to" or something similair.

#### Add weight to the card 
Next you have to add a so called weight to the card. This is used to depict the workload of said card. We use numbers <b>1, 2, 3, 5 and 8</b>. If you think your card has a weight of 8 you might need to split it into smaller cards. You can determine the weights by consulting a group mate or by playing scrum poker.

#### Add a label 
If your created card is something that needs to be researched add the "research" label to it by clicking next to the text and scrolling down to "labels".

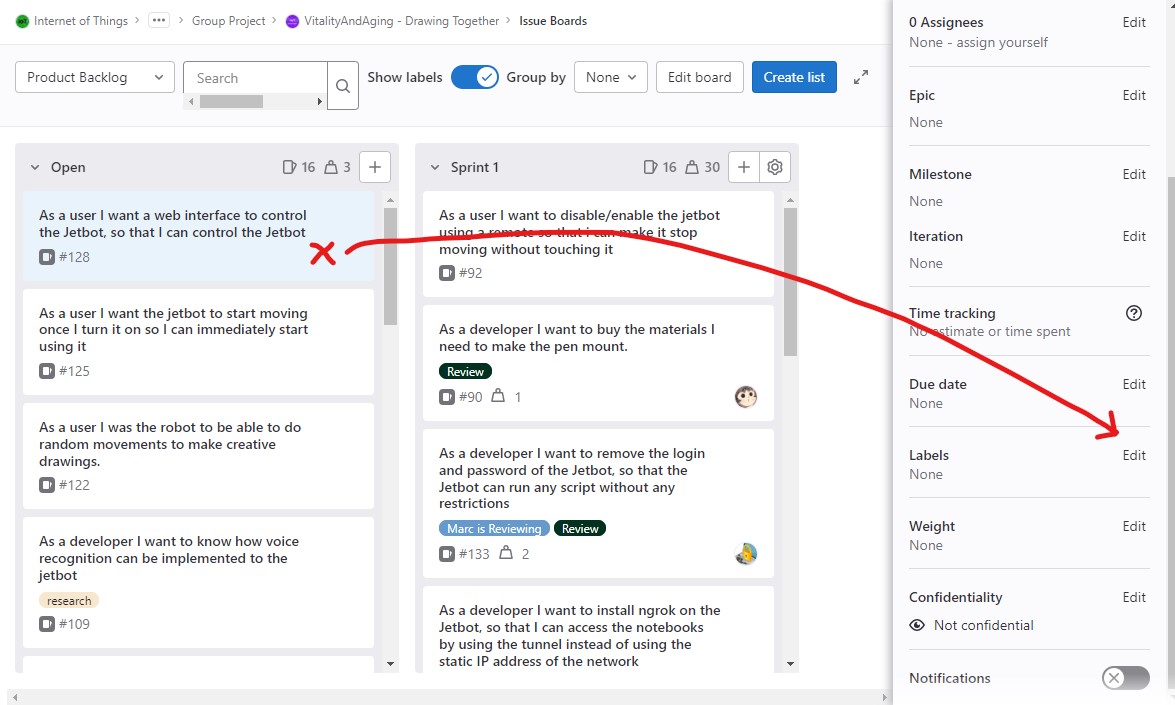
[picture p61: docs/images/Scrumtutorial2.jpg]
Step1D


## 2. Move the issue to a sprint
When the steps above have been completed you need to take the issue card to the sprint where the work is going to be done. To do this you click next to the text again and scroll down to <b>"milestone"</b>. Then click <b>edit</b> and select the sprint.

## 3. Work on the issue
#### Assign the issue
When it is time to work on the issue you can assign it to someone or to yourself. To do this you can click next to the text again and select the option where it says "0 assignees". Here you assign the person(s) that is/are completing the issue.

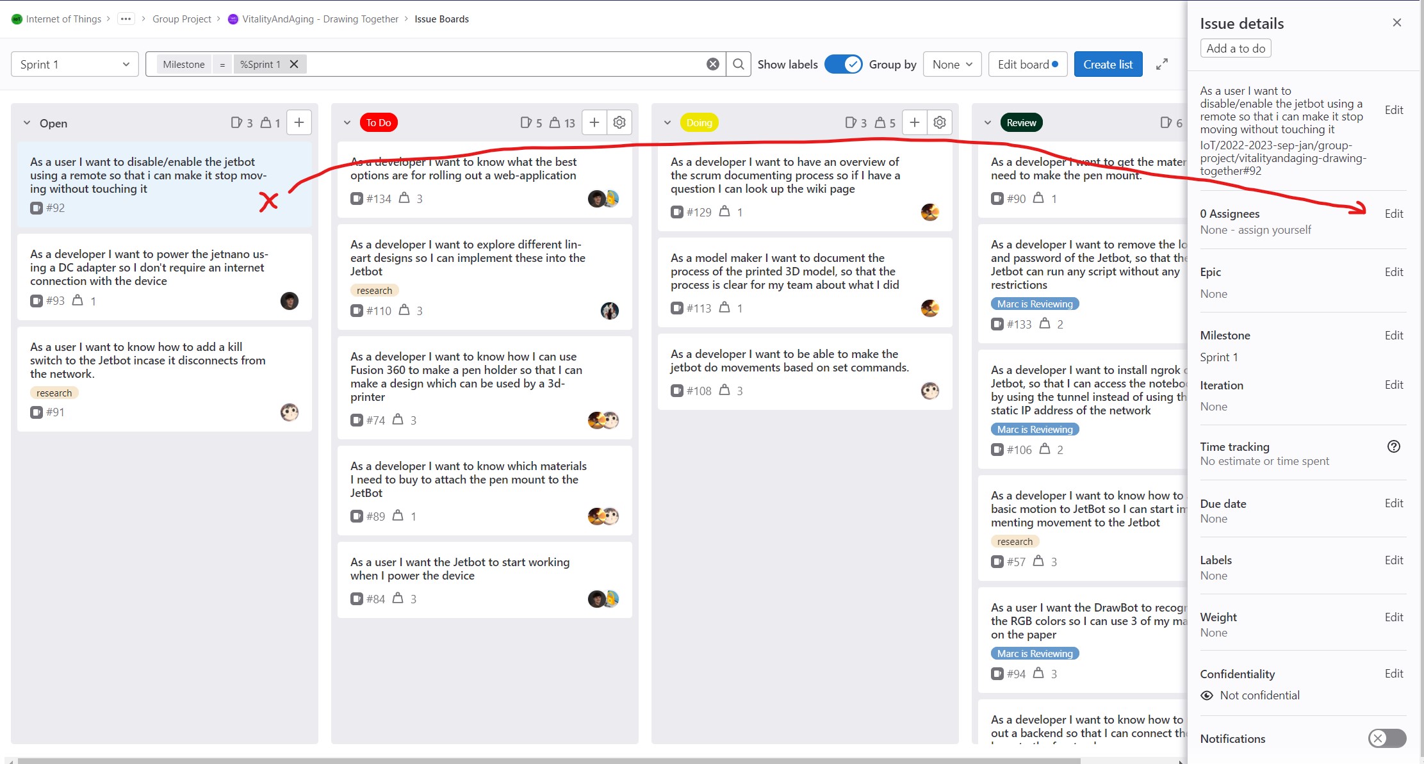
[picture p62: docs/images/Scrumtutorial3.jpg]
Step3A


#### To Do list
Once assigned you can drag the issue card into the "To Do" list. This means that the issue is going to be worked on <b>today</b> and <b>after the assignee has completed their previous issue</b>. When the latter is the case there needs to be a card with the same assignee in the "Doing" list.

#### Doing list
Is this list are all the cards that are currently being worked on. This "doing" can span multiple days depending on the weight. So you can leave the card in the "Doing" list if you continue the next day. Make sure to mention the in the standup.

#### Review list
When you have finished the issue and completed the [GIT](https://iot.dev.hihva.nl/2022-2023-sep-jan/group-project/vitalityandaging-drawing-together/git/git/) tutorial you drag the card from "Doing" to "Review" and you need to add a reviewer in the labels. The reviewer can be any of the groupmates. After that it is very important to add a link to the made work in the card so the reviewer can access it easily. This can be done by clicking on the text and adding a comment to the card.

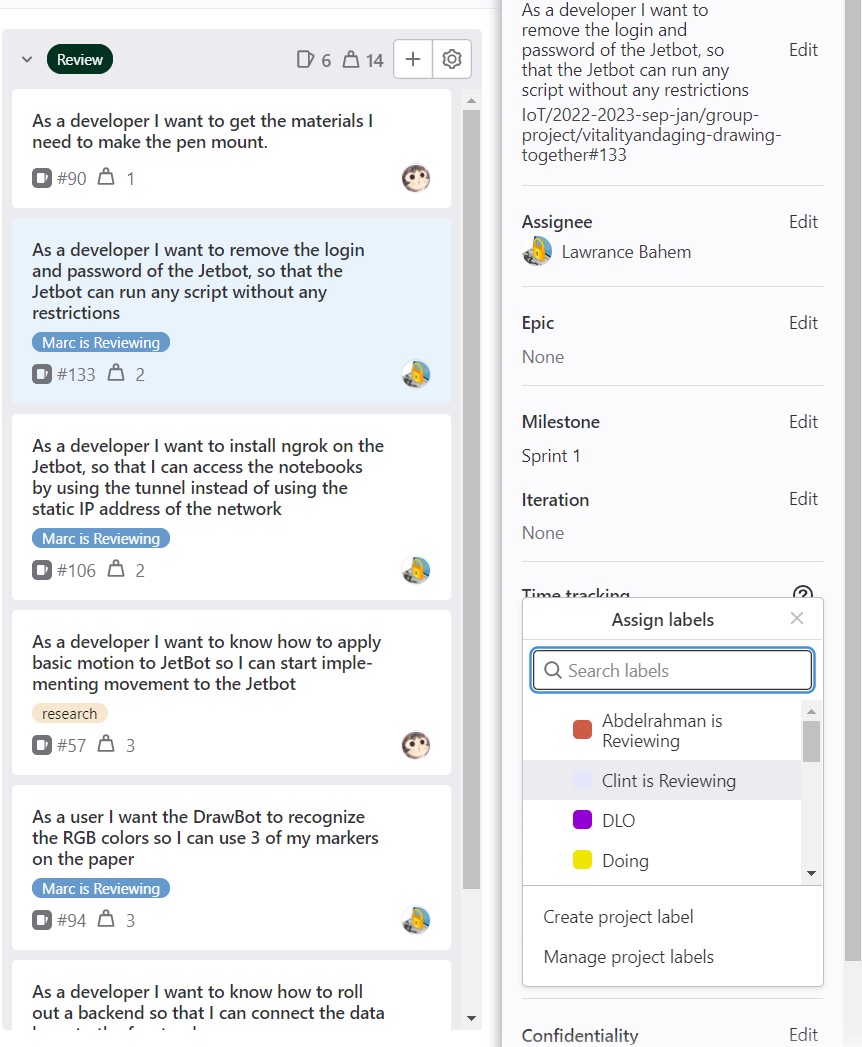
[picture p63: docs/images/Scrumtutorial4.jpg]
Step3D


## 4. Close the issue
When you are the assigned reveiwer you need to go through the work and check it for possible errors or things the creator did not see or could add. You also need to approve the merge request for the branches Develop and the branch created for the issue card.

For closing the issue, you don't need to do it manually. In the new templates for merge request, you should provide the following:

Link to the documentation (if there is any).
The issue number to have it closed once the merge request is approved by the reviewer.

Below are screenshots that show how the merge requests' templates work:

Documentation template:

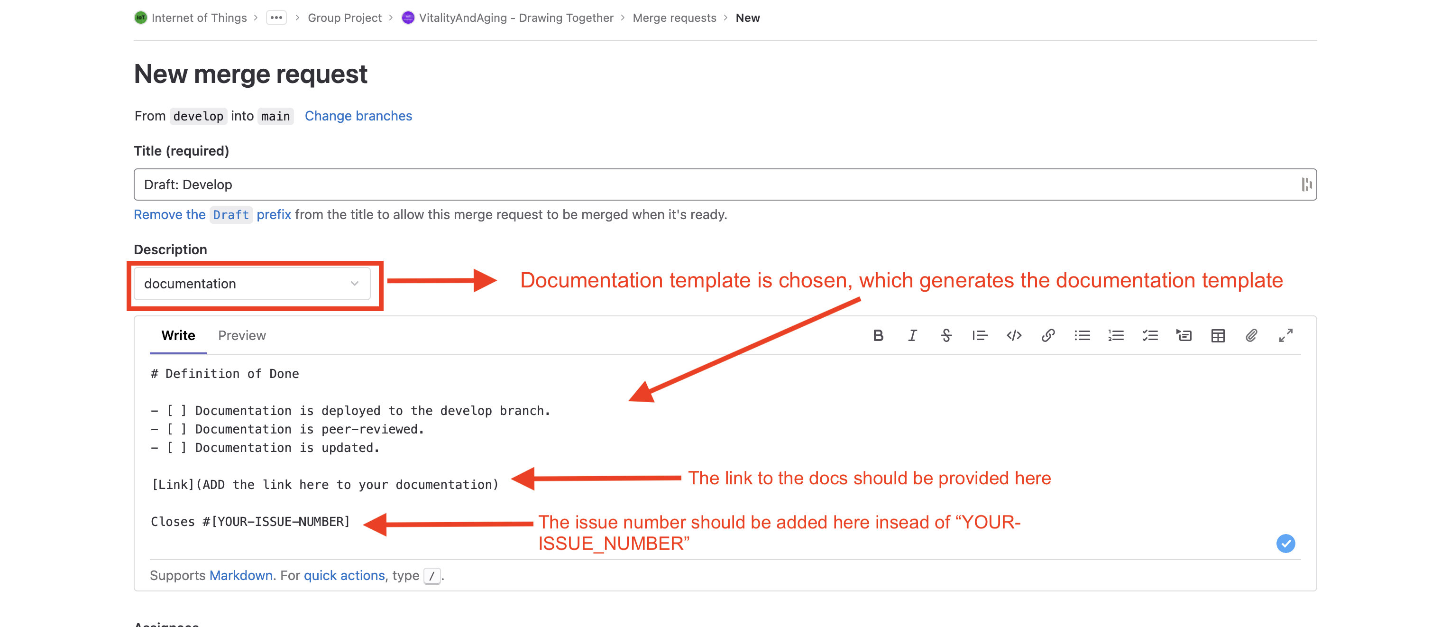
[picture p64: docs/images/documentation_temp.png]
</br>

Code template:

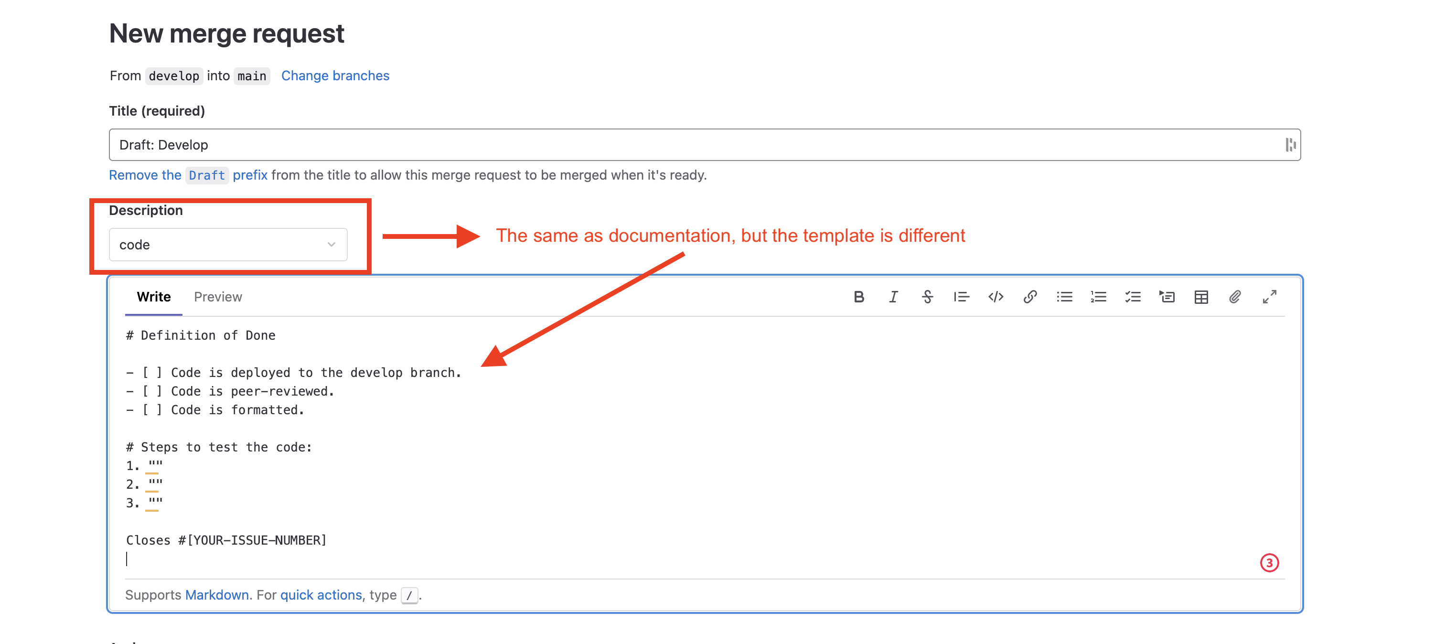
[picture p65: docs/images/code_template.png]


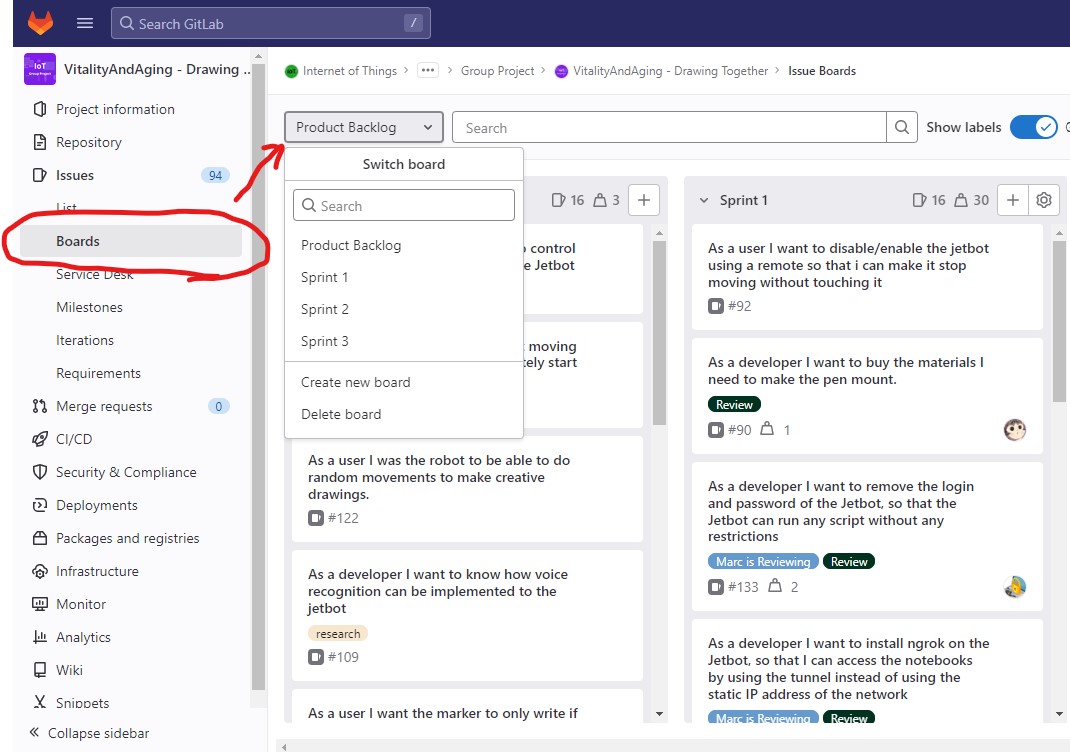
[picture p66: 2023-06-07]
docs/images/Scrumtutorial1.jpg

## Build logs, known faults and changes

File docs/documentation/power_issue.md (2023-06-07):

# Power issue

When loaded the Tensorflow model onto Jetson nano, we faced some troubles as not getting the Drawbot moving and
simultaneously recognizing shapes. That was due to the defeault configuration that the Jetson Nano uses, which resulted
in shutting down the Jetbot when loading the trained model.

Jetson systems are available in a variety of performance and power configurations. Most product development cycles
include balancing performance and power needs. Fortunately, NVIDIA has done the legwork and calculations to determine
which processing components deliver the optimum performance for a given energy budget in numerous combinations. At the
very least, these setups are an excellent place to start when creating your own tailored configuration.

Nvpmodel specifies the number of CPUs and their clock rates, as well as the GPU frequency and the External Memory
Controller (EMC) frequency. Keep in mind that the EMC regulates the speed of access to the external LPDDR4 memory.

The Jetson nano provides a far more robust computing environment than the Jetson TX2. The Xavier incorporates Deep
Learning Accelerators (DLA) and Visual Accelerators (VA) in addition to 4 additional CPU cores (VA). These new features
may also be customized using nvpmodel! nvpmodel defines four distinct power envelopes in seven distinct modes. The power
envelopes are 10 Watt, 15 Watt, 30 Watt, and "Forget power utilization, speed is what I need!".

The following table shows the seven different “modes” on the Jetson boards (it might differ for each board). The
following table breaks down the modes which describe which CPU, GPU, DLA and VA cores to use along with their clock
frequency, and the memory controller frequency.
<br>

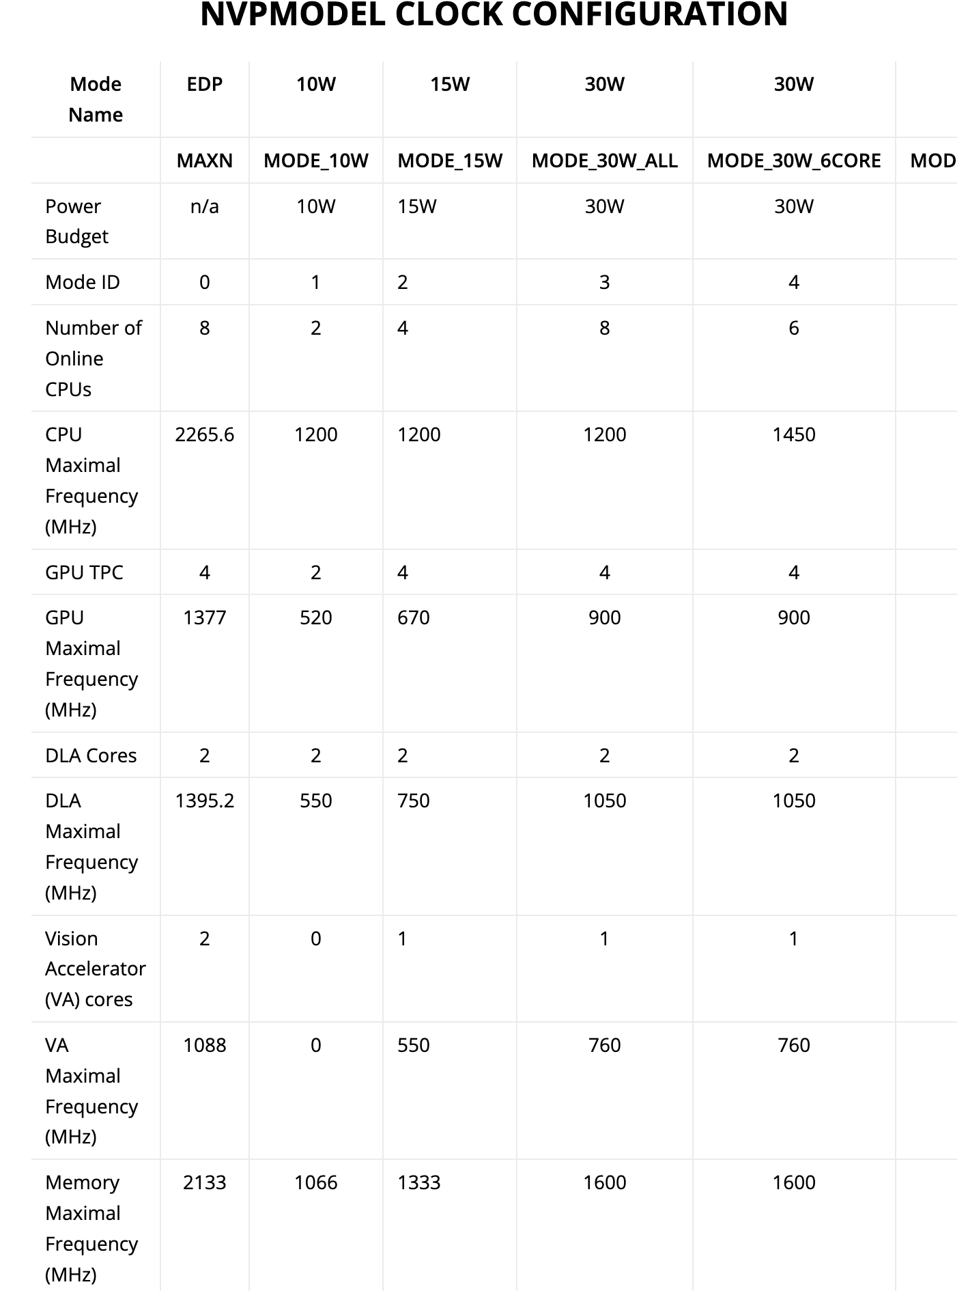
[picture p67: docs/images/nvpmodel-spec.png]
nvpmodel-spec


In short the following commands can be applied on the Jetson nano to reduce the power consumption among other things:

To call nvpmodel:

```bash
sudo nvpmodel -m [mode]
```

where mode is the number of the mode that you want to use. For example:

```bash
sudo nvpmodel -m 0
```

You can query which mode is currently being used:

```bash
sudo nvpmodel -q –verbose
```

In our case we have to set the Jetson power mode on 1, which uses 5 Watt.

```bash
sudo nvpmodel -m 1
```

Confirm the that the mode has been set to 5 Watt by executing the following command

```bash
sudo nvpmodel -q
```

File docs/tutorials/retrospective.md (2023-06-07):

# Sprint retrospective

## Useful links

[Online Sticky notes](https://lucid.app/lucidspark/4577a0c7-34e5-4871-8d7c-4092ed2ef513/edit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)

## How the retrospective goes down

Team gets together (preferrably in person). This will be done at the end of every sprint. Here the team discusses:

1. **What went well**  
We take 5 minutes to write down things that went well. Each item gets written on a sticky note. The notes will be placed on a board. After five minutes, the team removes duplicates and discusses the notes.

2. **What they would want to change**  
Next five minutes, the team writes down some more points on things they'd like to change (also 1 per note). When the time is up, duplicates are removed and action points are discussed.

3. **What actions they will take to improve future sprints**  
The team now has knowlegde on the scrum process from all team members. They will discuss and figure out what changes they want to make in the next sprint. These changes consist of SMART goals and are described in the sprint retrospective report

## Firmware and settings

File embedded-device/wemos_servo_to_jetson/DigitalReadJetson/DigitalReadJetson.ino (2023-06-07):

#define COMMAND_PIN D2
#define SERVO_PIN D4
#define SERVO_UP 0 
#define SERVO_DOWN 180 
#define SERIAL_ID 115200
#define START_DELAY 1000
#define LOOP_DELAY 100

#include <Servo.h>
Servo servo;

// the setup routine runs once when you press reset:
void setup() {
  Serial.begin(SERIAL_ID);
  pinMode(COMMAND_PIN, INPUT_PULLUP);
  servo.attach(SERVO_PIN);

  delay(START_DELAY);
  servo.write(SERVO_UP);
}

// the loop routine runs over and over again forever:
void loop() {
  // read the input pin:
  int inputState = digitalRead(COMMAND_PIN);
  // print out the state of the servo:
  Serial.println(inputState);
  if(inputState == HIGH){
    servo.write(SERVO_DOWN);
  } else if(inputState == LOW){
    servo.write(SERVO_UP);  
  }

  delay(LOOP_DELAY);
}

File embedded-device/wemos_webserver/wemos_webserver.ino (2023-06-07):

#include <ESP8266WiFi.h>
#include <ESP8266WebServer.h>

// Set WiFi credentials
#define WIFI_SSID "Drawbot"
#define WIFI_PASS "drawbot123"
#include <Servo.h>

int position = 0;
Servo servo_9;

// Create a new web server
ESP8266WebServer webserver(80);

// Handle Root
void setPenUp() {
  Serial.print("Set pen up has been called");
  servo_9.write(180);
  webserver.send(200, "text/json", "{\"isUp\": True}");
}

// Handle Root
void setPenDown() {
  Serial.print("Set pen down has been called");
  servo_9.write(0);
  webserver.send(200, "text/json", "{\"isUp\": False}");
}

// Handle 404
void notfoundPage() {
  webserver.send(404, "text/plain", "404: Not found");
}

void setup() {
  // Setup serial port
  Serial.begin(115200);
  Serial.println();
  servo_9.attach(D4);

  //Begin WiFi
  WiFi.begin(WIFI_SSID, WIFI_PASS);
  while (WiFi.status() != WL_CONNECTED) { delay(100); }

  // WiFi Connected
  Serial.print("Connected! IP address: ");
  Serial.println(WiFi.localIP());

  // Start Web Server
  webserver.on("/up", setPenUp);
  webserver.on("/down", setPenDown);

  webserver.onNotFound(notfoundPage);
  webserver.begin();
}

void loop() {
  webserver.handleClient();
}

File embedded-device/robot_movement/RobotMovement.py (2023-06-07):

from jetbot import Robot
import time
class RobotMovement(Robot):
    
    def __init__(self) -> None:
        super().__init__()
        
    def left_curve(self, speed):
        self.left_motor.value = speed / 2
        self.right_motor.value = speed
    
    def right_curve(self, speed):
        self.left_motor.value = speed / 2
        self.right_motor.value = speed
        
    def calculate_time(self, degree = 10):
        time = degree * 0.0109
        return time
        
    def turn_set_degrees_right(self, degree = 10, speed = 0.3):
        self.left_motor.value = speed
        self.right_motor.value = -speed
        timer = self.calculate_time(degree)
        time.sleep(timer)
        self.stop()
        
    def turn_set_degrees_left(self, degree = 10, speed = 0.3):
        self.left_motor.value = -speed
        self.right_motor.value = speed
        timer = self.calculate_time(degree)
        time.sleep(timer)
        self.stop()
        
    def turn_45_degree_right(self, speed = 0.3):
        self.left_motor.value = speed
        self.right_motor.value = -speed
        time.sleep(0.49)
        self.stop()
        
    def turn_45_degree_left(self, speed = 0.3):
        self.left_motor.value = -speed
        self.right_motor.value = speed
        time.sleep(0.49)
        self.stop()
        
    def turn_90_degree_right(self, speed = 0.3):
        self.left_motor.value = speed
        self.right_motor.value = -speed
        time.sleep(0.95)
        self.stop() 
        
    def turn_90_degree_left(self, speed = 0.3):
        self.left_motor.value = -speed
        self.right_motor.value = speed
        time.sleep(0.95)
        self.stop() 
        
    def turn_180_degree_right(self, speed = 0.3):
        self.left_motor.value = speed
        self.right_motor.value = -speed
        time.sleep(1.9)
        self.stop()
        
    def turn_180_degree_left(self, speed = 0.3):
        self.left_motor.value = -speed
        self.right_motor.value = speed
        time.sleep(1.9)
        self.stop()
        
    def turn_360_degree_right(self, speed = 0.3):
        self.left_motor.value = speed
        self.right_motor.value = -speed
        time.sleep(3.68)
        self.stop()
        
    def turn_360_degree_left(self, speed = 0.3):
        self.left_motor.value = -speed
        self.right_motor.value = speed
        time.sleep(3.68)
        self.stop()
        
        
    # ALl the curves at normal speeds.
    def right_curve_forward(self, speed = 0.3):
        self.left_motor.value = speed
        self.right_motor.value = speed / 2
        
    def left_curve_forward(self, speed = 0.3):
        self.left_motor.value = speed / 2
        self.right_motor.value = speed 
        
    def right_curve_backward(self, speed = -0.3):
        self.left_motor.value = speed
        self.right_motor.value = speed / 2
    
    def left_curve_backward(self, speed = -0.3):
        self.left_motor.value = speed / 2
        self.right_motor.value = speed 
        
    # ALl the curves at fast speeds.
    def right_curve_forward_fast(self, speed = 0.8):
        self.left_motor.value = speed
        self.right_motor.value = speed / 2
        
    def left_curve_forward_fast(self, speed = 0.8):
        self.left_motor.value = speed / 2
        self.right_motor.value = speed 
        
    def right_curve_backward_fast(self, speed = -0.8):
        self.left_motor.value = speed
        self.right_motor.value = speed / 2
    
    def left_curve_backward_fast(self, speed = -0.8):
        self.left_motor.value = speed / 2
        self.right_motor.value = speed
    
        
#     left_motor = traitlets.Instance(Motor)
#     right_motor = traitlets.Instance(Motor)

#     # config
#     i2c_bus = traitlets.Integer(default_value=1).tag(config=True)
#     left_motor_channel = traitlets.Integer(default_value=1).tag(config=True)
#     left_motor_alpha = traitlets.Float(default_value=1.0).tag(config=True)
#     right_motor_channel = traitlets.Integer(default_value=2).tag(config=True)
#     right_motor_alpha = traitlets.Float(default_value=1.0).tag(config=True)
    
#     def __init__(self, *args, **kwargs):
#         super(Robot, self).__init__(*args, **kwargs)
#         self.motor_driver = Adafruit_MotorHAT(i2c_bus=self.i2c_bus)
#         self.left_motor = Motor(self.motor_driver, channel=self.left_motor_channel, alpha=self.left_motor_alpha)
#         self.right_motor = Motor(self.motor_driver, channel=self.right_motor_channel, alpha=self.right_motor_alpha)
        
#     def set_motors(self, left_speed, right_speed):
#         self.left_motor.value = left_speed
#         self.right_motor.value = right_speed
        
#     def forward(self, speed=1.0, duration=None):
#         self.left_motor.value = speed
#         self.right_motor.value = speed

#     def backward(self, speed=1.0):
#         self.left_motor.value = -speed
#         self.right_motor.value = -speed

#     def left(self, speed=1.0):
#         self.left_motor.value = -speed
#         self.right_motor.value = speed

#     def right(self, speed=1.0):
#         self.left_motor.value = speed
#         self.right_motor.value = -speed

#     def stop(self):
#         self.left_motor.value = 0
#         self.right_motor.value = 0
        

    
